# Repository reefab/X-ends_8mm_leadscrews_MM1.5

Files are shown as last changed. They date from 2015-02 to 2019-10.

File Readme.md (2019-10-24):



# X-ends for MendelMax 1.5 for 8mm leadscrews and 8mm rods with wobble isolator

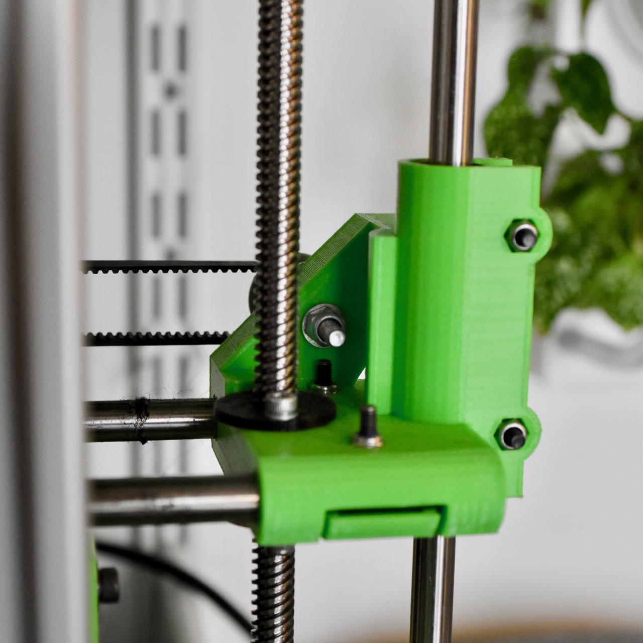
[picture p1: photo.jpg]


Based on [jonaskuehling's design](http://www.thingiverse.com/thing:18384) with the following modifications:

 * 8mm trapezoidal leadscrew. See the included [image](trapezoidal_screw.png) for mechanical specifications.
 * GT2 belt, the idler thus has a hole for a M4 bolt intended for two 624 ball bearings.
 * Z wobble isolator

The design was originally made for a Prusa i2 and had flexible coupling between the X and Z axis to prevent binding issues caused buy the flexible structure of the i2 and the parallelism issues that ensued.

As this does not happen on the rigid structure of a MendelMax, this tended to exacerbate the Z wobbling issue considering that the X-ends are in that case constrained by the leadscrews and not the smooth rods. Any misalignment issues are transfered to the X-Axis and ultimately the print itself.

To prevent that, I made it so that the leadscrew nut would be able to slightly slide along the X-Axis direction and removing flexibility between the X and Z axis.

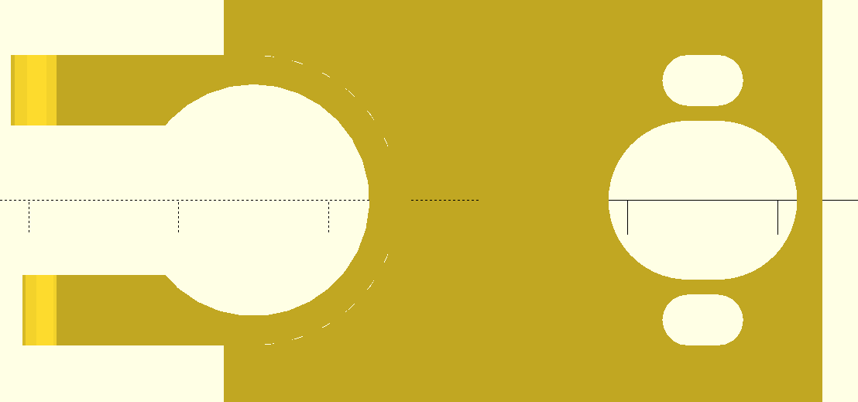
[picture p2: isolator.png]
isolator


## Instructions

 * Printed in PLA at 40% infill for rigidity
 * Clean up the leadscrew holes so that the leadscrew nut slides smoothly back and forth
 * insert the top_nut part on the other side of the leadscrew nut, secure both with m3 screws

You can use the "gauge" part to get the correct spacing between the motor spindle and the smooth rod.

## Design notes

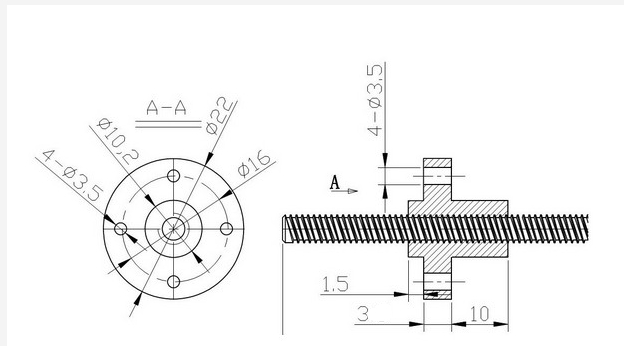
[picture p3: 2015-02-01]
trapezoidal_screw.png

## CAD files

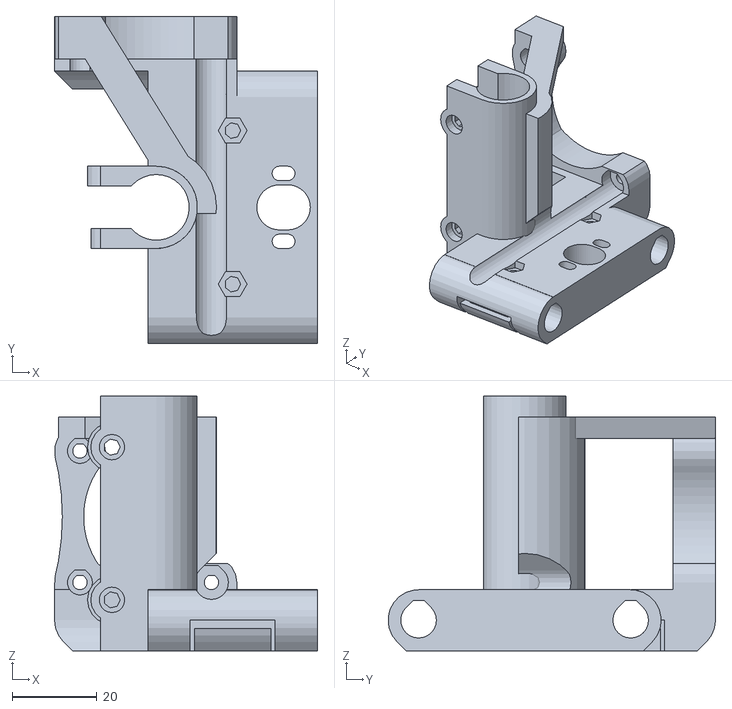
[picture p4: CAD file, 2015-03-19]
x-motor.stl
62.0 x 77.1 x 60.0

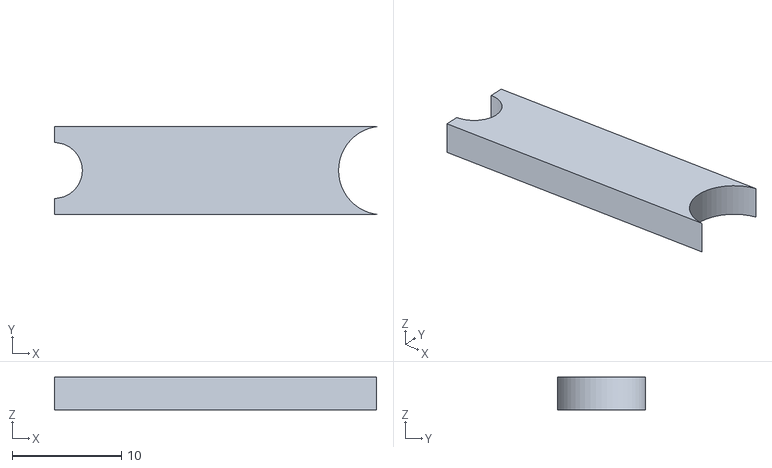
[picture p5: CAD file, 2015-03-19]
gauge.stl
29.4 x 8.00 x 3.00

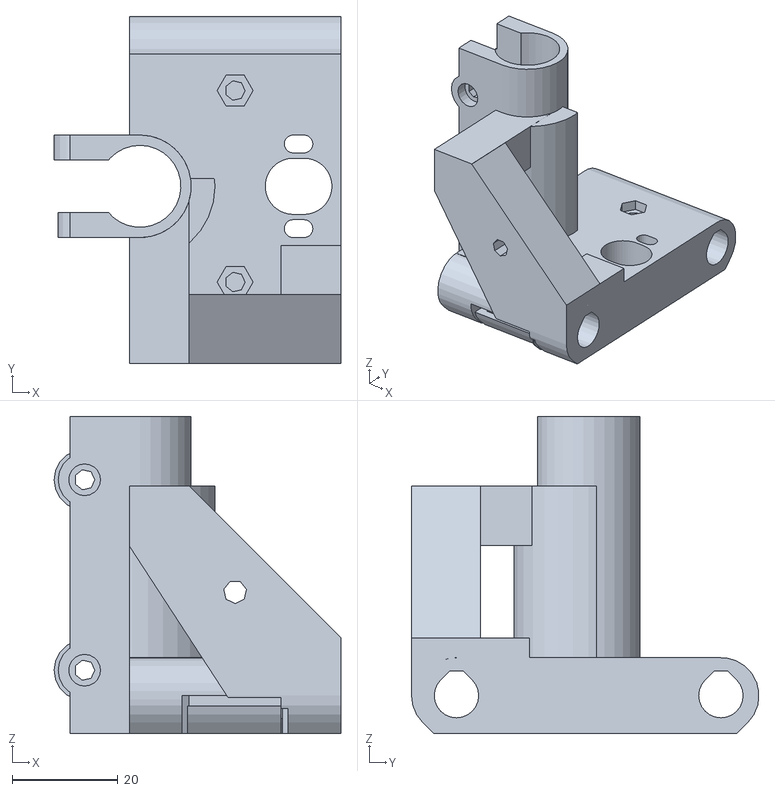
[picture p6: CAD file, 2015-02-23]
x-idler.stl
54.2 x 65.6 x 60.0

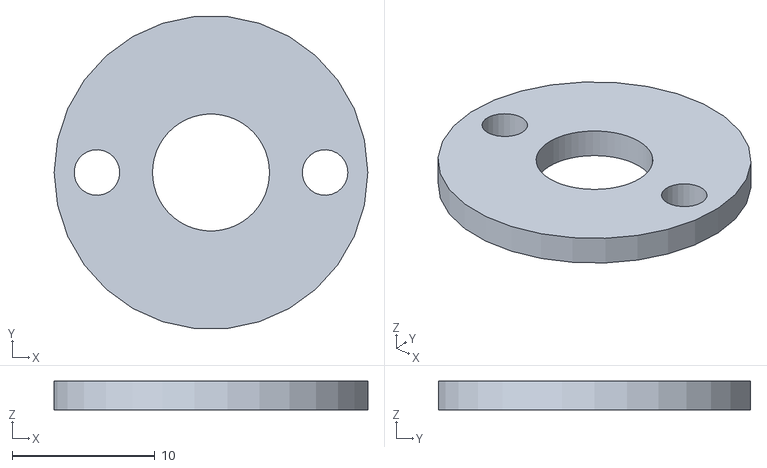
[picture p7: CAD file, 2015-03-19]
top_nut.stl
22.0 x 21.9 x 2.00

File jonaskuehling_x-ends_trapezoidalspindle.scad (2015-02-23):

use <jonaskuehling-default.scad>
include <lm8uu-holder-slim_double-vertical.scad>

// PARAMETERS
rod_dia = 8;
rod_dist = 50;		// center to center
zrod_leadscrew_dist = 30;
clearance = 0.2;		// default clearance
wall = 3;			// default wall thickness
wall_thin = 3;
xend_body_length = 40;

m3_screw_dia = 3;
m3_screw_head_dia = 5.5;
m3_screw_head_height = 3;
m3_nut_wrench_size = 5.5;
m3_nut_height = 2.4;

m4_screw_dia = 4;

m8_screw_dia = 8;
m8_washer_dia = 16;
m8_washer_height = 1.5;

idler_dia = 13;		// when using pure 608 bearing without belt guide: 22mm

belt_rod_dist = 7.5;		// in y direction
belt_elevation = 6.5;		// in z direction, space between rod top and belt bottom;
						// = distance between upper side of rods and upper platform of x-carriage (with belt clamps)
belt_height = 2.6;		// belt thickness..

xmotor_y_offset = 45;
idler_y_offset = rod_dist/2+rod_dia/2+belt_rod_dist - 2*m8_washer_height;

// belt range = rod_dist/2+rod_dia/2+belt_rod_dist - nema17 shaft socket = 36.5 - 43 = 6.5mm

leadscrew_dia = 8;
/*leadscrew_nut_wrench_size = 17+0.2;		// plus some extra clearance*/
/*anti_backlash_spring_space = 20;*/
leadscrew_nut_height = 10;
leadscrew_nut_inner_diameter = 10.2;
leadscrew_nut_outter_diameter = 22;
leadscrew_nut_hole_from_center = 8;

nema17_width = 43;
nema17_hole_dist = 31;
nema17_center_dia = 25;

layer_height = 0.2;

xend_body_x_offset = 3;
motor_mount_x_offset = -2;


// CALCULATIONS
xend_body_height = rod_dia+2*clearance+2*wall;
xend_body_width = rod_dist+rod_dia+2*wall;
leadscrew_nuttrap_height = 2*leadscrew_nut_height+wall+anti_backlash_spring_space;
bearing_support_height = leadscrew_nuttrap_height;
idler_elevation = xend_body_height/2+rod_dia/2+belt_elevation+belt_height+idler_dia/2;


// RENDER
// "idler=false" for motor-x-end, "idler=true" for idler-x-end
idler=true;

assembly(idler);

// -------------------------------------------------

module rod_mount(){
	difference(){
		// block for rods
		translate([0,(rod_dist/2+rod_dia/2+wall)/2,0])
			cube([xend_body_length,rod_dist/2+xend_body_height/2,xend_body_height],center=true);
	
		// round corners horizontal
		translate([xend_body_length/2,rod_dist/2+xend_body_height/2,xend_body_height/2])
			rotate([180,90,0])
				roundcorner(xend_body_height/2,xend_body_length);
		translate([xend_body_length/2,rod_dist/2+xend_body_height/2,-xend_body_height/2])
			rotate([0,0,180]) 
				roundcorner_tear(xend_body_height/2,xend_body_length);
	
		// rod hole
		translate([0,rod_dist/2,0]) teardropcentering(rod_dia/2+clearance,xend_body_length+2);
	
		// rod clamp
		translate([0,body_width/2+1,0])
		difference(){
			translate([0,(rod_dist/2+rod_dia/2+wall+1)/2,-(rod_dia/2+wall+1)/2])
				cube([xend_body_length-20,rod_dist/2+rod_dia/2+wall+1,rod_dia/2+wall+1],center=true);
			translate([0,(rod_dist/2+rod_dia/2+wall+1)/2,-(rod_dia/2+wall+1)/2-2])
				cube([xend_body_length-20-2,rod_dist/2+rod_dia/2+wall+1+2,rod_dia/2+wall+1],center=true);
		}
		translate([0,rod_dist/2,-0.1]) teardropcentering_half(rod_dia/2+clearance+1,xend_body_length-20-2-4,bottom=1);
		

		// clamp screw + nut trap + screw-head-trap
		translate([0,rod_dist/2-rod_dia/2-m3_screw_dia/2-2*clearance-1,0])
			polyhole(m3_screw_dia+2*clearance,xend_body_height+2);
		translate([0,rod_dist/2-rod_dia/2-m3_screw_dia/2-2*clearance-1,xend_body_height/2-m3_nut_height/2+0.5])
			nut_trap(m3_nut_wrench_size,m3_nut_height+1);
	}

	// screw hole print support
	translate([0,rod_dist/2-rod_dia/2-m3_screw_dia/2-2*clearance-1,layer_height/2+(xend_body_height/2-layer_height*round((xend_body_height/2)/layer_height))])
		polyhole(m3_screw_dia+2*clearance,layer_height);
}



module bearing_holder(){
	// linear bearing holder
	translate([-zrod_leadscrew_dist/2,0,0])
		rotate([0,0,90])
			lm8uu_holder_slim_double_vertical();
}

module bearing_holder_spacer(){
	render()
	/*translate([-body_width/2-zrod_leadscrew_dist/2 - 5,0,body_length/2])*/
	/*	 # cube([body_width,body_width+3,body_length+2], center = true);*/
	difference(){
		translate([-zrod_leadscrew_dist/2,0,-1])
			 cylinder(r=body_width/2, h=body_length+2);
		translate([body_width/2-zrod_leadscrew_dist/2+body_width/2-0.5,0,body_length/2])
			 cube([body_width,body_width+3,body_length+2], center = true);
	}
}



module leadscrew_nuttrap(){
	translate([zrod_leadscrew_dist/2,0,0])
		rotate([0,0,30]){
			translate([0,0,leadscrew_nuttrap_height/2])
				difference(){
					nut_trap(leadscrew_nut_wrench_size+2*wall,leadscrew_nuttrap_height);
					nut_trap(leadscrew_nut_wrench_size,leadscrew_nuttrap_height+2);
				}
			translate([0,0,wall/2+leadscrew_nut_height])
				difference(){
					nut_trap(leadscrew_nut_wrench_size+2*wall,wall);
					rotate([0,0,-30]) cube([leadscrew_dia+1,leadscrew_nut_wrench_size*2,wall+2],center=true);
				}
		}
}




nema17_hole1 = [nema17_hole_dist/2,nema17_hole_dist/2];
nema17_hole2 = [nema17_hole_dist/2,-nema17_hole_dist/2];
nema17_hole3 = [-nema17_hole_dist/2,nema17_hole_dist/2];
nema17_hole4 = [-nema17_hole_dist/2,-nema17_hole_dist/2];

module motor_mount(){
	difference(){
		union(){
			translate([-nema17_hole_dist/2+motor_mount_x_offset,xmotor_y_offset,
						nema17_hole_dist/2+xend_body_height+m3_screw_dia/2+clearance])
				difference(){
					union(){
						rotate([90,0,0])
							linear_extrude(height=10){
								barbell(nema17_hole3,nema17_hole4,
										(nema17_width-nema17_hole_dist)/2,(nema17_width-nema17_hole_dist)/2,
										20,60);
								barbell(nema17_hole4,nema17_hole2,
										(nema17_width-nema17_hole_dist)/2,(nema17_width-nema17_hole_dist)/2,
										20,60);
							}
		
						// nema17 mount bottom support
						translate([0,-10-(xmotor_y_offset-10-rod_dist/2)/2,
									-xend_body_height/2-nema17_hole_dist/2-m3_screw_dia/2-clearance])
							cube([nema17_width,xmotor_y_offset-10-rod_dist/2,xend_body_height],center=true);
						translate([0,-5,-(xend_body_height+m3_screw_dia/2+clearance)/2-nema17_hole_dist/2])
							difference(){
								cube([nema17_width,10,(xend_body_height+m3_screw_dia/2+clearance)],center=true);

								// round corner bottom x direction
								translate([nema17_width/2,5,-(xend_body_height+m3_screw_dia/2+clearance)/2])
									rotate([0,0,180]) 
										roundcorner_tear(xend_body_height/2,nema17_width);
							}
					}
		
					// nema17 screw holes
					for(k=[1,-1]) for(l=[1,-1])
						translate([k*nema17_hole_dist/2,-5,l*nema17_hole_dist/2])
							rotate([0,0,90]) teardrop(m3_screw_dia/2+clearance,12);
		
					// xend body cut off 1
					translate([0,-(xmotor_y_offset-rod_dist/2)-0.1,-(xend_body_height/2+m3_screw_dia/2+clearance)-nema17_hole_dist/2])
						rotate([180,0,0])
							teardropcentering(xend_body_height/2,nema17_width+2);

					// round corner bottom y direction
					translate([-nema17_width/2,5,-nema17_hole_dist/2-m3_screw_dia/2-clearance-xend_body_height])
						rotate([0,0,-90]) 
							roundcorner_tear(xend_body_height/2,nema17_width);
				}
		
			// nema17 mount top support
			translate([0,0,nema17_hole_dist+(m3_screw_head_dia+2*clearance)/2+xend_body_height+m3_screw_dia/2+clearance])
				linear_extrude(height=5)
					polygon(points=[[-xend_body_length/2+xend_body_x_offset,body_width/2+1.5],[-xend_body_length/2+xend_body_x_offset+10,body_width/2+1.5],
										[-nema17_hole_dist+motor_mount_x_offset+5,xmotor_y_offset],
										[-nema17_hole_dist+motor_mount_x_offset-5,xmotor_y_offset]]);

			translate([-nema17_hole_dist+motor_mount_x_offset,-5+xmotor_y_offset,nema17_hole_dist+xend_body_height+m3_screw_dia/2+clearance+(5+m3_screw_head_dia/2+clearance)/2])
				cube([10,10,5+m3_screw_head_dia/2+clearance],center=true);

			difference(){
				union(){
					translate([-body_width/2-zrod_leadscrew_dist/2,0,(nema17_hole_dist+(m3_screw_head_dia+2*clearance)/2+xend_body_height+m3_screw_dia/2+clearance+5)/2])
						cube([body_width,body_width+3+2*wall,nema17_hole_dist+(m3_screw_head_dia+2*clearance)/2+xend_body_height+m3_screw_dia/2+clearance+5], center=true);
					translate([-zrod_leadscrew_dist/2,0,0])
						cylinder(r=body_width/2+1.5+wall, h=nema17_hole_dist+(m3_screw_head_dia+2*clearance)/2+xend_body_height+m3_screw_dia/2+clearance+5);
				}
				/*# translate([-(body_width+1)/2-zrod_leadscrew_dist/2,0,body_length/2])*/
				/*	cube([body_width+1,body_width+3,body_length+2], center = true);*/
				translate([-zrod_leadscrew_dist/2,0,-1])
					cylinder(r=body_width/2, h=body_length+2);
				 translate([-body_width-xend_body_length/2+xend_body_x_offset,0,body_length/2])
					cube([2*body_width,body_width+3+2*wall+2,body_length+2], center = true);
				translate([xend_body_x_offset,-xend_body_width/4-wall/2,body_length/2])
					cube([xend_body_length+2,xend_body_width/2,body_length+2], center = true);
			}
		}

		// xend body cut off 2
		translate([-xend_body_length+xend_body_x_offset,rod_dist/2-0.1,xend_body_height])
			cube([xend_body_length,xend_body_height,xend_body_height],center=true);
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

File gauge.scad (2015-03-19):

rod_dia = 8;
motor_shaft_dia = 5;
clearance = 0.1;

zrod_leadscrew_dist = 30;

height = 3;

difference() {
    translate([0,0,height/2]) cube([zrod_leadscrew_dist, rod_dia, height], center=true);

    translate([zrod_leadscrew_dist/2,0,0]) cylinder(d=rod_dia + clearance, h=height, $fn=50);
    translate([-zrod_leadscrew_dist/2,0,0]) cylinder(d=motor_shaft_dia + clearance, h=height, $fn=25);
}

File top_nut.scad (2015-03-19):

leadscrew_nut_inner_diameter = 10.2;
leadscrew_nut_outter_diameter = 22;
leadscrew_nut_hole_from_center = 8;
leadscrew_dia = 8;
clearance = 0.2;
m3_screw_dia = 3;

difference() {
    cylinder(d=leadscrew_nut_outter_diameter, h=2);
    union() {
        for (i=[-1, 1]) translate([i* leadscrew_nut_hole_from_center,0,0]) cylinder(d=m3_screw_dia + clearance, h=2, $fn=25);
        cylinder(d=leadscrew_dia + clearance, h=2, $fn=50);
    }
}

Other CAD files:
jonaskuehling-default.scad
lm8uu-holder-slim_double-vertical.scad

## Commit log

2015-02-01 Initial import
    [jonaskuehling-default.scad, jonaskuehling_x-ends_threadedrod.scad, jonaskuehling_x-ends_trapezoidalspindle.scad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]
2015-02-01 Holes for leadscrew nut + smaller idler bolt hole
    [jonaskuehling_x-ends_trapezoidalspindle.scad]
2015-02-01 idler diameter for 624 bearing
    [jonaskuehling_x-ends_trapezoidalspindle.scad]
2015-02-01 bigger idler mount
    [jonaskuehling_x-ends_trapezoidalspindle.scad]
2015-02-01 bigger back idler mount
    [jonaskuehling_x-ends_trapezoidalspindle.scad]
2015-02-01 Preparing for publication
    [jonaskuehling_x-ends_threadedrod.scad, jonaskuehling_x-ends_trapezoidalspindle.scad, x-idler.stl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]
2015-02-06 Reverted idler mount modifications
    [jonaskuehling_x-ends_trapezoidalspindle.scad]
2015-02-06 Modified nut mounting holes
    [jonaskuehling_x-ends_trapezoidalspindle.scad, x-idler.stl, x-motor.stl]
2015-02-07 Much beefier idler mount to compensate for the m4 bolt
    [jonaskuehling_x-ends_trapezoidalspindle.scad]
2015-02-07 Exported STL
    [x-idler.stl, x-motor.stl]
2015-02-08 Lowered top idler mount
    [jonaskuehling_x-ends_trapezoidalspindle.scad]
2015-02-23 Removed bearing holder isolators
    [jonaskuehling_x-ends_trapezoidalspindle.scad]
2015-02-23 reinforced bearing mount on idler side
    [jonaskuehling_x-ends_trapezoidalspindle.scad]
2015-02-23 Reinforced bearing mount on motor side
    [jonaskuehling_x-ends_trapezoidalspindle.scad]
2015-02-23 Added isolator
    [jonaskuehling_x-ends_trapezoidalspindle.scad]
2015-02-23 reduced idler support bottom
    [jonaskuehling_x-ends_trapezoidalspindle.scad]
2015-02-23 stl files exported
    [x-idler.stl, x-motor.stl]
2015-03-19 Added documentation and images
    [gauge.scad, gauge.stl, top_nut.scad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]
